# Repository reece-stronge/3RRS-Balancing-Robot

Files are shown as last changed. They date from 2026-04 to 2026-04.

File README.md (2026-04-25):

# 3-RRS Ball Balancing Robot 

<video src="https://github.com/user-attachments/assets/cb008f77-76ea-4a3e-9e36-dd4379848b34" width="100" controls></video>

## 🎯 Overview

This repository contains the software and other relevant materials from my MEng final year project, a 3-RRS moving platform that autonomously balances a ball and tracks dynamic setpoints in real time. To achieve this, the project combines inverse kinematics with mechanical design, classical control theory, real-time computer vision and software development, which culminated in a multi-threaded, event-synchronised software architecture that uses PID control to correct the ball's position using camera feedback.

## ⚙️ Hardware and Dependencies
|No|Component|Quantity|Purpose|
|---|---|---|---|
|1|Savox SA-1258TG Coreless Digital Servo|3|Actuators|
|2|PCA9685 Servo Driver|1|Servo PWM Control
|3|Raspberry Pi 5|1|Host Controller|
|4|Raspberry Pi 5 Active Cooler|1|Cooling|
|5|Raspberry Pi Camera Module 3 Wide|1|Object Detection with CV|
|6|22-way 0.5mm-pitch to 15-way 1mm-pitch FPC Camera Cable|1|Camera module to Pi 5 MIPI connection|
|7|SA5T/K M5x0.8 Rod End Bearing|3|Spherical Joints|
|8|625RS 5x16x5 (5mm I.D.) Ball Bearing|3|Revolute Joints|
|9|6V, 5A External Power Supply|1|Servo Power|

### Software Dependencies
- Python, OpenCV, NumPy, Matplotlib, picamera2, Adafruit ServoKit, pynput, threading

## 📏 CAD Files
All original bodies found in the CAD directory were newly designed in Autodesk Fusion and can be 3D printed/lasercut.  
Note the lower links were specifically designed to fit the particular servo horns used for this project.

## 🖥️ MATLAB Kinematics Simulation
Separate functions define the sets of equations to calculate the necessary motor angle for each leg individually based on a desired orientation.  
Desired platform pose is defined as its centre height, tilt magnitude and tilt direction in the main solver script, which calculates the necessary motor angles and plots them in 3D vector space to ensure a physically logical pose.  
This static pose generation was directly translated from MATLAB into the Python environment on the Raspberry Pi in `inverse_kinematics.py`.

## ⌨️ Keyboard Manual Control
    keyboard_control.py
Provides open-loop, discrete manual control of the platform's orientation using threaded keyboard listening to map the positional variables to pre-defined keystrokes:  
Height: W/S | Tilt Magnitude: ↑/↓ | Tilt Direction: ←/→  
Listening for keyboard input on a separate background thread from the kinematics solver allows them to run in parallel and not interfere with one another.

## ⭕ Fixed Trajectory Following
    fixed_trajectory.py
Commands the platform to continuously follow a pre-defined trajectory - tilt direction is continuously incremented through 360 degrees while maintaining a fixed height and tilt magnitude.  
Calculates the execution time of the kinematics when running continuously.

## 👁️ Computer Vision Calibration
    camera_tuning.py
A tuning environment that provides a GUI with trackbars for the user to calibrate the necessary HSV colour thresholds to detect the ball, along with preview windows for the subsequent binary mask and contour bounding box computed by the OpenCV algorithms. 

## 🎯 Main Balancing Program
    main.py | pose.py | pid.py | camera.py
The core application of the project, responsible for the real-time closed-loop stabilisation of the ball. To separate the concerns the system is modularised into four distinct components:
- `main.py`: The main execution loop that manages event-driven thread synchronisation, executes the main control loop and handles end-of-run data logging and plotting.
- `camera.py`: Interfaces with the camera module to execute the OpenCV colour masking and contour detection algorithms.
- `pid.py`: Houses the PID control theory to compute the necessary tilt magnitude and direction and applies EMA low-lass filtering (currently disabled for this project via `a = 1` in `main.py`).
- `pose.py`: Translates the required control effort into physical actuation via the inverse kinematics solver and I2C servo commands.
### Configuration Notes
- **Colour Thresholds:** The HSV colour bounds used to detect the ball are hardcoded within the `Camera` class in `camera.py`. The correct thresholds for the current lighting environment/ball colour can be identified using `camera_tuning.py` and the arrays in `camera.py` can be updated accordingly.
- **Step Response Testing:** To analyse dynamic tracking performance, a predefined step response can be triggered by setting the `ENABLE_STEP_RESPONSE` boolean to `True` within `main.py`. The specific target pixel coordinates and timing intervals for the sequence are manually configured inside the main loop.

## 🚀 Installation and Usage
**1. Create and activate a virtual environment**  
This project was run inside a Python virtual environment to prevent package conflicts on the Raspberry Pi. This is now the required standard for Raspberry Pi OS Bookworm which the Raspberry Pi 5 runs. Within a terminal:  
```
python3 -m venv --system-site-packages ~/.venv
source ~/.venv/bin/activate
```
**2. Install dependencies**  
With the virtual environment activated, install the required packages e.g:
```
pip install adafruit-circuitpython-servokit
```
_(picamera2 is typically pre-installed on modern Raspberry Pi OS releases, but may require specific system configuration to enable)_  
  
**3. Usage**  
With the hardware connected and virtual environment activated, the scripts can be opened and executed directly within a Python IDE like Thonny that comes pre-installed on the Raspberry Pi OS.

## PyBullet Physics Engine Simulation
```
balance_sim.py
```
A "digital twin" constructed in the PyBullet rigid-body physics engine for system validation. It uses approximations of the physics of a ping-pong ball rolling on an acrylic plate along with a 1:1 mirror of the `PID` class in `pid.py` and the measured end-to-end hardware latency of the real system to isolate the performance of the controller. Different initial conditions as well as a step response can be enabled by adjusting the relevant variables.  
  


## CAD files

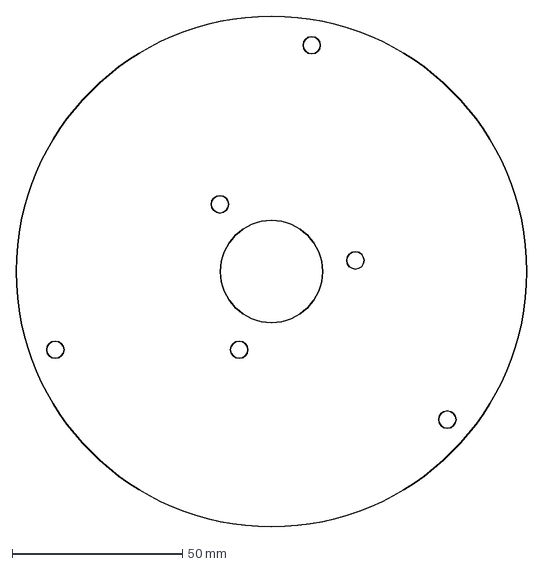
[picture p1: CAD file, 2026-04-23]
cad/Base_Plate.dxf
150.0 x 150.0 mm

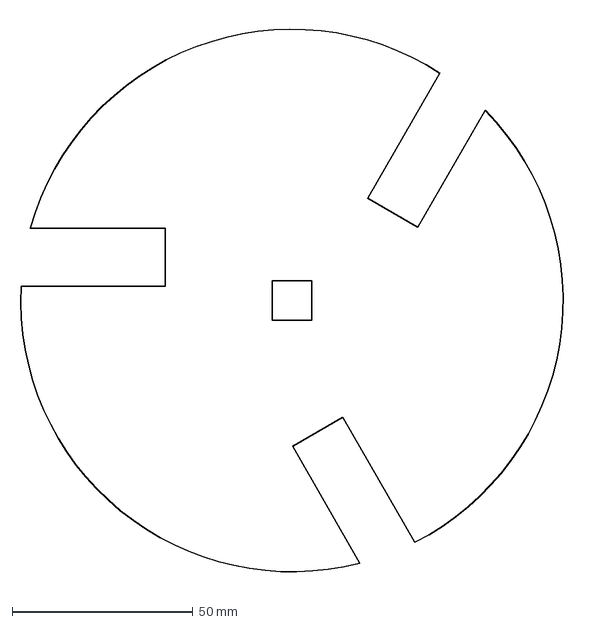
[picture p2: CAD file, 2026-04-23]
cad/Mid_Plate.dxf
154.0 x 157.2 mm

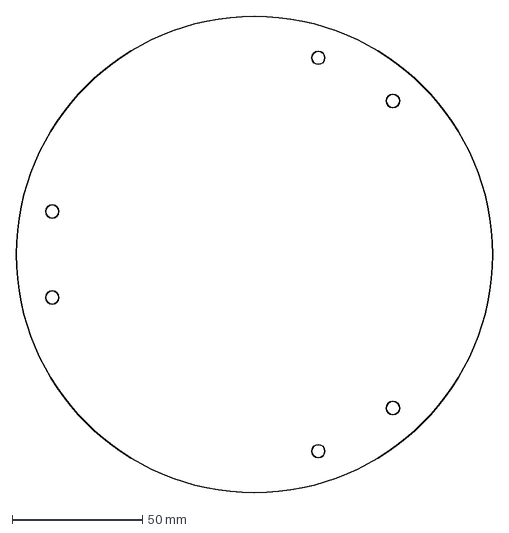
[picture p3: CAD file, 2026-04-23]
cad/Top_Platform.dxf
182.5 x 182.5 mm

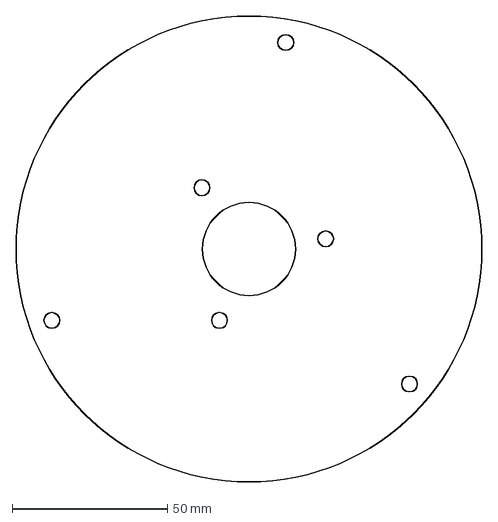
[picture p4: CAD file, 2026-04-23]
CAD/Base DXF.dxf
150.0 x 150.0 mm

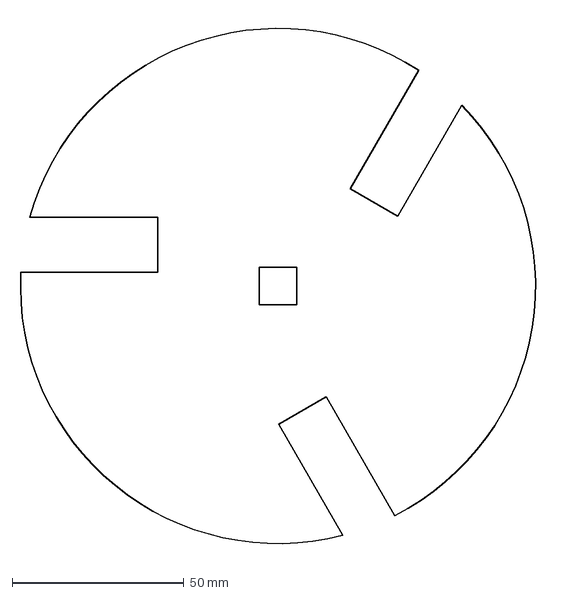
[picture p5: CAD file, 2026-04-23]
CAD/Mid Plate DXF.dxf
154.0 x 157.2 mm

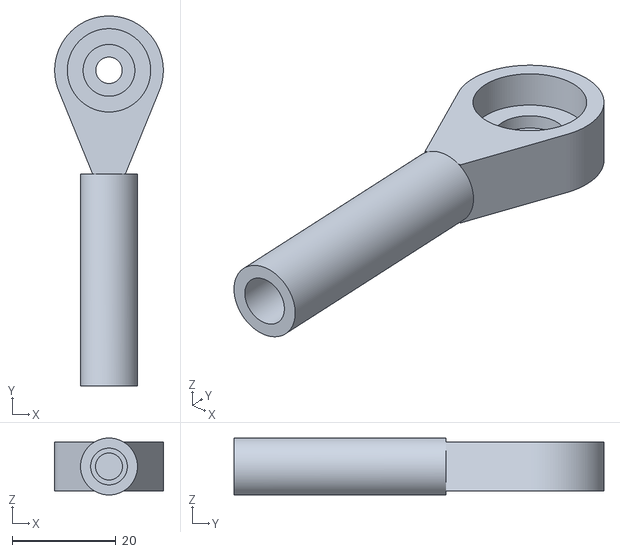
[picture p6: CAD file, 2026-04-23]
cad/Upper_Link.stl
21.0 x 71.5 x 11.0

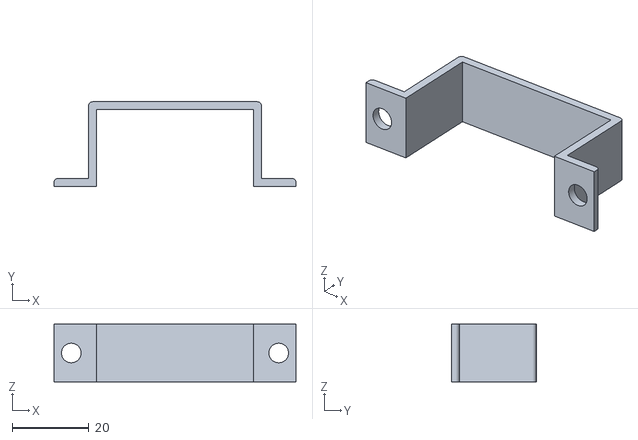
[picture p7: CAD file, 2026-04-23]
cad/Motor_Bracket.stl
63.0 x 22.0 x 15.0

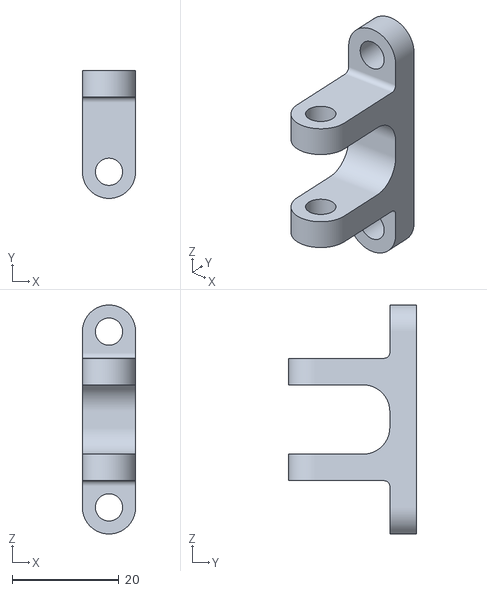
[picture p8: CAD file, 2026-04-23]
cad/Spherical_Attachment.stl
10.0 x 24.0 x 43.0

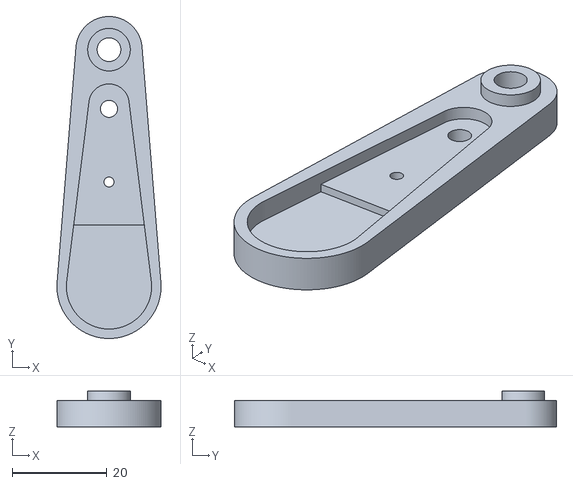
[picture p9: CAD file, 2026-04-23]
cad/Lower_Link.stl
22.0 x 68.0 x 7.50

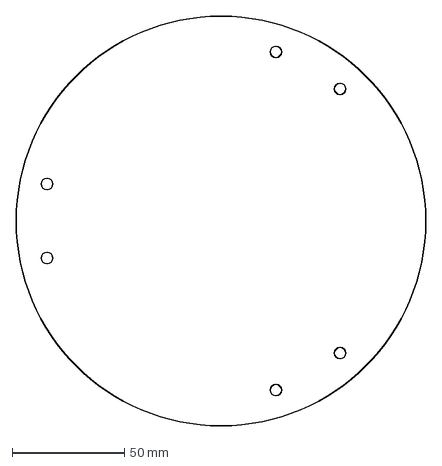
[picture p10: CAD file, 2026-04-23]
CAD/Top Plate.dxf
182.5 x 182.5 mm

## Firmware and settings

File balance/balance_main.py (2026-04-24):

import time
import cv2
import numpy as np
import threading
import matplotlib.pyplot as plt

# Import modules
from pose import Pose
from pid import PID
from camera import Camera

# --- Global Setup Variables ---
height = 480
width = 480
channels = 3
image = np.zeros((height, width, channels), dtype=np.uint8)

k_scale = 1
K_PID = [0.018, 0.0015, 0.01]
a = 1

# Step Response Toggle
ENABLE_STEP_RESPONSE = False

Platform = Pose()
camera_module = Camera()
pid = PID(K_PID, k_scale, a)

Platform.initialize_platform()
h_ini = Platform.ini_pos[2]

running = True
x = -1
y = -1
area = -1
goal = [0, 0]

log_time = []
log_error_x = []
log_error_y = []
log_cv_time = []
log_pos_x = []
log_pos_y = []
log_goal_x = []
log_goal_y = []
log_ctrl_time = []
log_s1 = []
log_s2 = []
log_s3 = []
latest_cv_time = 0.0
plot_start_time = time.time()

def main():
    global running
    
    image_event = threading.Event()
    data_event = threading.Event()
    
    def get_img():
        global image
        while running:
            image = camera_module.take_pic()
            image_event.set()

    def control_robot():
        global x, y, area, latest_cv_time
        while running:
            
            image_event.wait()
            if not running:
                break
            image_event.clear()
            
            # --- Start CV Stopwatch ---
            t_start_cv = time.perf_counter()
            
            x, y, area = camera_module.find_object(image)
            
            # --- End CV Stopwatch ---
            t_end_cv = time.perf_counter()
            latest_cv_time = (t_end_cv - t_start_cv) * 1000
            
            data_event.set()

    try:
        camera_thread = threading.Thread(target=get_img)
        robot_thread = threading.Thread(target=control_robot)
        camera_thread.start()
        robot_thread.start()

        while running:
            
            data_event.wait()
            data_event.clear()
            
            current_pos = [x, y, area]
            
            # Safe camera monitoring - Main thread for GUI safety
            cv2.imshow("Debug Feed", image)
            
            # Exit logic
            key = cv2.waitKey(1) & 0xFF
            if key == ord('q'):
                running = False
                break
            
            if x != -1:
                
                current_time = time.time() - plot_start_time
                
                # --- Dynamic setpoint (Step Response) ---
                if ENABLE_STEP_RESPONSE:
                    if current_time < 15.0:
                        goal = [0, 0]
                    elif current_time < 25.0:
                        goal = [0, 200]
                    elif current_time < 35.0:
                        goal = [0, -200]
                    else:
                        goal = [0, 0]
                else:
                    goal = [0, 0]
                    
                logged_error_x = goal[0] - current_pos[0]
                logged_error_y = goal[1] - current_pos[1]
                
                log_time.append(current_time)
                log_error_x.append(logged_error_x)
                log_error_y.append(logged_error_y)
                log_pos_x.append(current_pos[0])
                log_pos_y.append(current_pos[1])
                log_goal_x.append(goal[0])
                log_goal_y.append(goal[1])
                
                # --- Start control stopwatch ---
                t_start_ctrl = time.perf_counter()
                
                tilt_phi, tilt_theta = pid.compute(goal, current_pos)
                pos = [tilt_phi, tilt_theta, h_ini]
                
                # No sleep time needed - timed by event wait
                s1, s2, s3 = Platform.pose_platform(pos, 0)
                
                # --- End control stopwatch ---
                t_end_ctrl = time.perf_counter()
                ctrl_time = (t_end_ctrl - t_start_ctrl) * 1000
                
                log_cv_time.append(latest_cv_time)
                log_ctrl_time.append(ctrl_time)
                
                # --- Log commanded angles ---
                log_s1.append(s1)
                log_s2.append(s2)
                log_s3.append(s3)
            else:
                pass

    finally:
        
        print("Stopping threads...")
        running = False
        
        image_event.set()
        data_event.set()
        
        if camera_thread.is_alive():
            camera_thread.join()
        if robot_thread.is_alive():
            robot_thread.join()
            
        # --- Reset platform pose ---
        Platform.pose_platform([0, 0, 0.11], 0.5)
        
        print("Stop and generate plots")
        Platform.clean_up()
        camera_module.clean_up_cam()
        
        if len(log_time) > 0:
            # Plot 1 - Error Response
            plt.figure(1, figsize=(10, 6))
            plt.plot(log_time, log_error_x, label='X Axis Error', color='blue', alpha=0.7)
            plt.plot(log_time, log_error_y, label='Y Axis Error', color='red', alpha=0.7)
            plt.axhline(0, color='black', linestyle='--', linewidth=1)
            plt.title('PID Response: Error vs Time')
            plt.xlabel('Time (s)')
            plt.ylabel('Error (px)')
            plt.legend()
            plt.grid(True)
            plt.savefig('error_plot.png')
            
            # Plot 2 - Commanded Motor Angles
            plt.figure(2, figsize=(10, 6))
            plt.plot(log_time, log_s1, label='Servo 1', color='red', alpha=0.8, linewidth=1)
            plt.plot(log_time, log_s2, label='Servo 2', color='green', alpha=0.8, linewidth=1)
            plt.plot(log_time, log_s3, label='Servo 3', color='blue', alpha=0.8, linewidth=1)
            plt.title('Control Effort: Commanded Motor Angles (Sync Threads)')
            plt.xlabel('Time (s)')
            plt.ylabel('Commanded Angle (Degrees)')
            plt.legend()
            plt.grid(True)
            plt.savefig('angles_plot.png')
            
            # Plot 3 - Absolute Position (Step Response)
            plt.figure(3, figsize=(10, 6))
            plt.plot(log_time, log_goal_x, label='X Target', color='black', linestyle='--', linewidth=1.5)
            plt.plot(log_time, log_goal_y, label='Y Target', color='grey', linestyle='--', linewidth=1.5)
            plt.plot(log_time, log_pos_x, label='X Position', color='blue', alpha=0.7)
            plt.plot(log_time, log_pos_y, label='Y Position', color='red', alpha=0.7)
            plt.title('System Step Response: Position Tracking')
            plt.xlabel('Time (s)')
            plt.ylabel('Position (px from centre)')
            plt.legend()
            plt.grid(True)
            plt.savefig('step_response.png')
            
        else:
            print("No data recorded to plot")
            
        # Plot 3 - Computational Load (Execution Times)
        if len(log_cv_time) > 0:
            plt.figure(4, figsize=(10, 6))
            plt.plot(log_time, log_cv_time, label='Computer Vision Execution', color='purple', alpha=0.8)
            plt.plot(log_time, log_ctrl_time, label='PID and Kinematics Execution', color='orange', alpha=0.8)
            avg_cv = sum(log_cv_time) / len(log_cv_time)
            avg_ctrl = sum(log_ctrl_time) / len(log_ctrl_time)
            plt.title(f'System Execution Time Breakdown: Avg CV: {avg_cv:.2f}ms Avg Control: {avg_ctrl:.2f}ms')
            plt.xlabel('Time (s)')
            plt.ylabel('Execution Time (ms)')
            plt.legend()
            plt.grid(True)
            plt.savefig('execution_times.png')
        
        plt.show()

if __name__ == "__main__":
    main()

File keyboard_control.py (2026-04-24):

import numpy as np
import time
from adafruit_servokit import ServoKit
from pynput import keyboard

# --- Geometry & Calibration ---
L, L1, L2, L3 = 0.09125, 0.075, 0.05, 0.075
servo1_0, servo2_0, servo3_0 = 40, 22, 20

# --- Initial State ---
h = 0.122
tilt_theta = 0.0
tilt_phi = 0.0

# Step sizes for control
H_STEP = 0.001     # 1mm change
TILT_STEP = 0.5    # 0.5 degree change
PHI_STEP = 2.0     # 2.0 degree change

# Track which keys are pressed
pressed_keys = set()

# --- Leg functions ---
def leg1_angle(n, h, L, L1, L2, L3):
    den_sqrt = np.sqrt(n[0]**2 + n[2]**2)
    a1 = (L/den_sqrt)*n[2]
    b1 = 0
    c1 = h + (L/den_sqrt)*(-n[0])
    S1 = np.array([a1, b1, c1])
    A = (L3 - S1[0]) / S1[2]
    B = (S1[0]**2 + S1[1]**2 + S1[2]**2 - L1**2 - L3**2 + L2**2) / (2 * S1[2])
    C = A**2 + 1
    D = 2*(A*B - L3)
    E = B**2 + L3**2 - L2**2
    x1 = (-D + np.sqrt(D**2 - 4*C*E)) / (2*C)
    y1 = 0
    z1 = np.sqrt(L2**2 - x1**2 + 2*L3*x1 - L3**2)
    P1 = np.array([x1, y1, z1])
    angle1 = 90 - np.degrees(np.arctan2(P1[0]-L3, P1[2]))
    return angle1

def leg2_angle(n, h, L, L1, L2, L3):
    common_denom = np.sqrt(n[0]**2 + 3*n[1]**2 + 4*n[2]**2 + 2*np.sqrt(3)*n[0]*n[1])
    a2 = (L/common_denom)*(-n[2])
    b2 = (L/common_denom)*(-np.sqrt(3)*n[2])
    c2 = h + (L/common_denom)*(np.sqrt(3)*n[1] + n[0])
    S2 = np.array([a2, b2, c2])
    A2 = -(S2[0] + np.sqrt(3)*S2[1] + 2*L3) / S2[2]
    B2 = (S2[0]**2 + S2[1]**2 + S2[2]**2 + L2**2 - L1**2 - L3**2) / (2*S2[2])
    C2 = A2**2 + 4
    D2 = 2*A2*B2 + 4*L3
    E2 = B2**2 + L3**2 - L2**2
    x2 = (-D2 - np.sqrt(D2**2 - 4*C2*E2)) / (2*C2)
    y2 = np.sqrt(3) * x2
    z2 = np.sqrt(L2**2 - 4*x2**2 - 4*L3*x2 - L3**2)
    P2 = np.array([x2, y2, z2])
    angle2 = 90 - np.degrees(np.arctan2(np.sqrt(P2[0]**2 + P2[1]**2) - L3, P2[2]))
    return angle2

def leg3_angle(n, h, L, L1, L2, L3):
    common_denom = np.sqrt(n[0]**2 + 3*n[1]**2 + 4*n[2]**2 - 2*np.sqrt(3)*n[0]*n[1])
    a3 = (L/common_denom)*(-n[2])
    b3 = (L/common_denom)*(np.sqrt(3)*n[2])
    c3 = h + (L/common_denom)*(-np.sqrt(3)*n[1] + n[0])
    S3 = np.array([a3, b3, c3])
    A3 = -(S3[0] - np.sqrt(3)*S3[1] + 2*L3) / S3[2]
    B3 = (S3[0]**2 + S3[1]**2 + S3[2]**2 + L2**2 - L1**2 - L3**2) / (2*S3[2])
    C3 = A3**2 + 4
    D3 = 2*A3*B3 + 4*L3
    E3 = B3**2 + L3**2 - L2**2
    x3 = (-D3 - np.sqrt(D3**2 - 4*C3*E3)) / (2*C3)
    y3 = -np.sqrt(3)*x3
    z3 = np.sqrt(L2**2 - 4*x3**2 - 4*L3*x3 - L3**2)
    P3 = np.array([x3, y3, z3])
    angle3 = 90 - np.degrees(np.arctan2(np.sqrt(P3[0]**2 + P3[1]**2) - L3, P3[2]))
    return angle3

# --- Servo Setup ---
kit = ServoKit(channels=16)
servos = [kit.servo[0], kit.servo[1], kit.servo[2]]

# --- Keyboard Handling ---
def on_press(key):
    try: pressed_keys.add(key.char)
    except AttributeError: pressed_keys.add(key)

def on_release(key):
    try: pressed_keys.remove(key.char)
    except (AttributeError, KeyError): 
        if key in pressed_keys: pressed_keys.remove(key)

# Start keyboard listener in background
listener = keyboard.Listener(on_press=on_press, on_release=on_release)
listener.start()

print("Control started. Use:")
print("W/S: Height | UP/DOWN: Tilt Magnitude | LEFT/RIGHT: Tilt Direction | ESC: Quit")

try:
    while True:
        # 1. Update variables based on held keys
        if 'w' in pressed_keys: h += H_STEP
        if 's' in pressed_keys: h -= H_STEP
        if keyboard.Key.up in pressed_keys: tilt_theta += TILT_STEP
        if keyboard.Key.down in pressed_keys: tilt_theta -= TILT_STEP
        if keyboard.Key.right in pressed_keys: tilt_phi += PHI_STEP
        if keyboard.Key.left in pressed_keys: tilt_phi -= PHI_STEP
        
        # Constrain variables
        tilt_theta = np.clip(tilt_theta, 0, 20)
        h = np.clip(h, 0.08, 0.1228)
        
        # 2. Re-calculate Normal Vector
        tr, pr = np.radians(tilt_theta), np.radians(tilt_phi)
        n = np.array([np.sin(tr)*np.cos(pr), np.sin(tr)*np.sin(pr), np.cos(tr)])
        
        # 3. Calculate and Move
        try:
            a1 = leg1_angle(n, h, L, L1, L2, L3)
            a2 = leg2_angle(n, h, L, L1, L2, L3)
            a3 = leg3_angle(n, h, L, L1, L2, L3)
            
            servos[0].angle = np.clip(servo1_0 + a1, 0, 180)
            servos[1].angle = np.clip(servo2_0 + a2, 0, 180)
            servos[2].angle = np.clip(servo3_0 + a3, 0, 180)
        except:
            pass # Skip frame if math is out of bounds
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

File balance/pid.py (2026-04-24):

import time
import numpy as np

class PID:
    def __init__(self, K_PID, k_scale, alpha):
        self.kp = K_PID[0]
        self.ki = K_PID[1]
        self.kd = K_PID[2]
        self.k_scale = k_scale
        self.alpha = alpha
        
        self.last_output_x = 0
        self.last_output_y = 0
        self.last_derivative_x = 0
        self.last_derivative_y = 0
        self.last_error_x = 0
        self.integral_x = 0
        self.last_error_y = 0
        self.integral_y = 0
        self.last_time = None
        self.count = 0

    def compute(self, Target, current_pos):
        current_time = time.perf_counter()
        if self.last_time is None:
            self.last_time = current_time
            return 0, 0
        
        error_x = Target[0] - current_pos[0]
        error_y = Target[1] - current_pos[1]
        
        self.integral_x += error_x * (current_time - self.last_time)
        self.integral_y += error_y * (current_time - self.last_time)
        
        raw_derivative_x = (error_x - self.last_error_x) / (current_time - self.last_time)
        raw_derivative_y = (error_y - self.last_error_y) / (current_time - self.last_time)
        
        # EMA filter on strictly derivative term
        derivative_x = self.alpha * raw_derivative_x + (1 - self.alpha) * self.last_derivative_x
        derivative_y = self.alpha * raw_derivative_y + (1 - self.alpha) * self.last_derivative_y
        
        output_x = self.kp * error_x + self.ki * self.integral_x + self.kd * derivative_x
        output_y = self.kp * error_y + self.ki * self.integral_y + self.kd * derivative_y
        
        ''' EMA Filter on entire controller outputs
        output_x = self.alpha * output_x + (1 - self.alpha) * self.last_output_x
        output_y = self.alpha * output_y + (1 - self.alpha) * self.last_output_y
        '''
        
        # Calculate direction (phi)
        tilt_phi = np.degrees(np.arctan2(output_y, output_x))
        if tilt_phi < 0:
            tilt_phi += 360
            
        # Calculate magnitude (theta)
        tilt_theta = self.k_scale * np.hypot(output_x, output_y)
        
        self.last_derivative_x = derivative_x
        self.last_derivative_y = derivative_y
        self.last_error_x = error_x
        self.last_error_y = error_y
        self.last_output_x = output_x
        self.last_output_y = output_y
        self.last_time = current_time

        return tilt_phi, tilt_theta

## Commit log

2026-04-23 Add CAD Files
2026-04-24 Renamed directories
    [Base_Plate.dxf, Lower_Link.stl, Mid_Plate.dxf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]
